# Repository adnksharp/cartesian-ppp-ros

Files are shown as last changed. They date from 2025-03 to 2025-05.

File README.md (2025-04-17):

# Cartesian Robot (PPP) ROS2

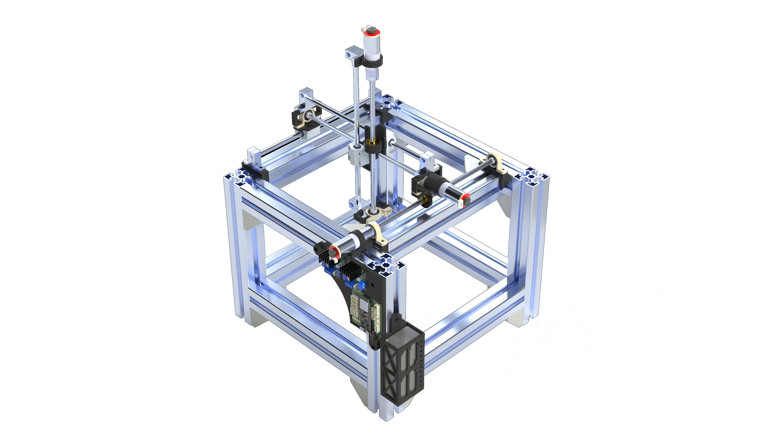
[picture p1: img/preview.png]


Robot cartesiano de 3 DOF con ROS2,

## Software y Hardware

<details>
    <summary>Software</summary>

* [ROS2 Jazzy](https://index.ros.org/p/desktop_full/#jazzy)
* [Gazebo Harmonic](https://gazebosim.org/docs/harmonic/getstarted/)
* [uROS Jazzy](https://github.com/micro-ROS/micro_ros_setup/tree/jazzy)
* [uROS Arduino Jazzy](https://github.com/micro-ROS/micro_ros_arduino/tree/jazzy)
* [KiCad](https://www.kicad.org)

</details>

<details>
    <summary>Componentes electrónicos</summary>

* 1 [ESP32 S3 WROOM 1 N16R8 DevKit](https://www.amazon.com/HiLetgo-ESP32-S3-ESP32-S3-DevKit-Bluetooth-Development/dp/B0CDWXWXCG)
* 2 [Módulos controladores de motores L298N](https://www.amazon.com/WWZMDiB-L298N-H-Bridge-Controller-Raspberry/dp/B0CR6BX5QL)
* 3 [Motores con encoder JGA25-371](https://www.amazon.com/JGA25-371-Encoder-Mounting-Bracket-Reduction/dp/B0CGLSGSZ7)
* 4 [LEDs 5730](https://www.amazon.com/AEDIKO-Lighting-Electronics-Components-Emitting/dp/B09XB5KDWS)
* 4 [Resistencias 220 Ohms 1206](https://www.amazon.com/Chanzon-Resistor-Tolerance-Resistors-Certificated/dp/B08R8CW7TX)
* 1 Fuente de alimentación 12V 2A

</details>

<details>
    <summary>Componentes mecánicos</summary>

* 12 perfiles de aluminio de 45x45x300 mm.
* 16 ángulos de aluminio de 45x45 mm.
* 3 tuercas de latón T8.
* 3 tornillos sin fin de 8x300 mm.
* 3 varillas lisas de 8x300 mm.
* 3 rodamientos SC8UU.
* 3 acopladores flexibles de 5x8 mm.
* 5 chumaceras KP08.
* 6 soportes SK8.
* Piezas impresas en 3D.

</details>

## Instalación
Para instalar el software de ROS2 Jazzy, se recomienda seguir la guía oficial de instalación de [ROS2](https://docs.ros.org/en/jazzy/Installation/Ubuntu-Install-Debs.html), el siguiente script instala el software de ROS2, Gazebo sim y micro-ROS en Ubuntu:

```shell
$SHELL ./src/install-ros.sh
```



Más información sobre el script en [src](src).

## Espacio de Trabajo de ROS2
Dentro de la carpeta ros-ws se encuentra el paquete en desarrollo `carobot`, el cual contiene los archivos para la visualización y simulación del robot cartesiano en Gazebo y RViz.

### Construcción del espacio de trabajo

```shell
cd ros-ws
colcon build
```

### Ejecución del lanzador

```shell
source install/setup.$(echo $SHELL | awk -F '/' '{print $NF}')
ros2 launch carobot display.launch.py
```

### Ejecución de la interfaz de usuario

```shell
source install/setup.$(echo $SHELL | awk -F '/' '{print $NF}')
ros2 run carobot pos_put.py
```

[ros-ws](ros-ws) contiene más información sobre el espacio de trabajo de ROS2.

## Electrónica
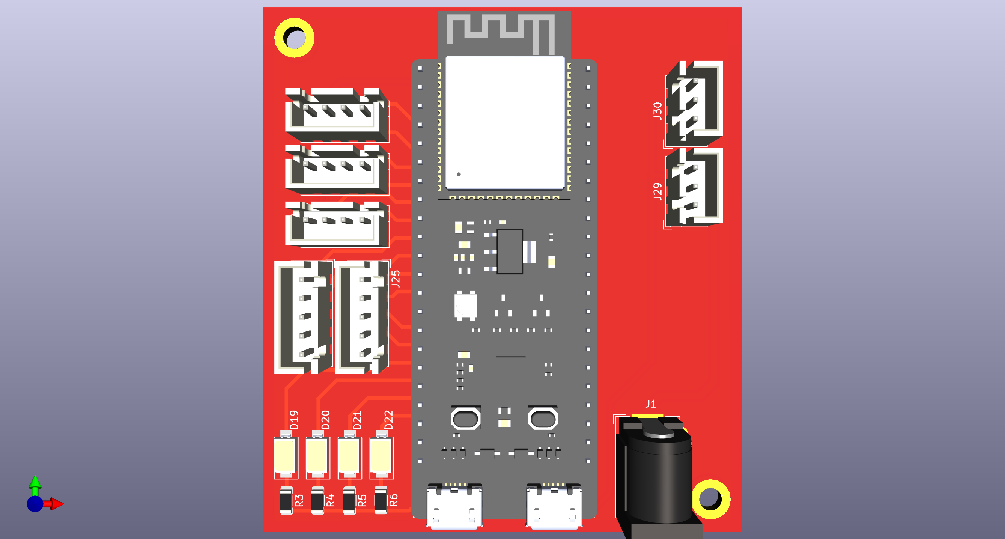
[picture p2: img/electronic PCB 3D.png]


[electronic](electronic) contiene el diseño de la PCB del robot cartesiano en formato KiCad, el cual incluye el diseño de la PCB y el esquema eléctrico.

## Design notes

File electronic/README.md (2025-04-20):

# Esquema elctrónico


El proyecto se desarrolló usando [KiCAD](https://www.kicad.org/). ([electronic.kicad_pro](electronic.kicad_pro)) se desarrollo para conectar una placa de ESP32 con 2 controladores de motores L298 y encoders de 3 motores JGA25-371. Los componentes utilizados en el proyecto son:

* 1 **ESP32 S3** WROOM 1 N16R8 DevKit
* 2 Modulos controladores de motores **L298**
* 3 Motores con encoder **JGA25-371**
* 4 LEDs
* 4 Resistencias **220 $\Omega$**
* 1 Fuente de alimentación **12V 2A**

## Esquema


El esquema eléctrico se encuentra dividido en ocho partes:

* 1 Alimentación: En esta sección se encuentra el conector de la fuente de alimentación para el circuito.
* 3 Motores
* 1 LED: LEDS conectados a los pines GPIO del microcontrolador y resistencias de 220 $\Omega$.
* 2 Controladores de motores
* 1 Microcontrolador

### Motores
En esta sección se encuentran los motores con encoder **JGA25-371**. 

* Las etiquetas del encoder se conectan a los pines GPIO del microcontrolador.
* Las etiquetas de alimentación se conectan a la salida de 3.3V del microcontrolador.
* Las etiquetas de los motores se conectan a los controladores de motores.

### Controladores de motores
En esta sección se encuentran los módulos de controladores de motores **L298N**. 

* Las etiquetas de los pines de control de los módulos se conectan a los pines GPIO del microcontrolador.
* Las etiquetas de alimentación se conectan a la fuente de alimentación y la salida de 5V de los controladores a la alimentación del microcontrolador.
* Las etiquetas de los motores se conectan a los motores.

### Microcontrolador
En esta sección se encuentra el microcontrolador **ESP32 S3** y las etiquetas de los pines que se utilizan para la comunicación con el resto de los componentes.

## PCB


La PCB fue diseñada para conectar todos los componentes del circuito. La PCB tiene un tamaño de 68.5x75 mm y fue diseñada para ser fabricada en dos capas. El diseño se encuentra en la carpeta `electronic` ([PCB.kicad_pcb](PCB.kicad_pcb)). Para la PCB se usan los siguientes componentes:

* 1 PCB de dos capas
* 1 Conector de alimentación **Barrel Jack**
* 2 Conectores **JST-B3B** para la alimentación de los controladores de motores.
* 3 Conectores **JST-B4B** para la conexión de los encoders de los motores.
* 2 Conectores **JST-B5B** para la conexión de los pines de control de los controladores de motores.
* 1 Terminal de 44 pines para la conexión del microcontrolador.
* 4 LEDs SMD **5730**
* 4 Resistencias 220 $\Omega$ SMD **1206**

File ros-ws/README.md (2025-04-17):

# Espacio de trabajo de ROS2


## carobot
El paquete `carobot` es un paquete de ROS2 para visualizar y simular el robot usando RViz2 y Gazebo. Este paquete incluye un modelo de robot y un archivo de lanzamiento.

### URDF
El modelo del robot se encuentra en el archivo `src/carobot/urdf/model.urdf`. Este archivo describe la geometría y la cinemática del robot. Las mallas usadas en el modelo se encuentran en la carpeta `src/carobot/urdf/meshes`. El archivo `model.urdf` es un archivo XML que describe el modelo del robot. Este archivo es usado por RViz2 y Gazebo para visualizar el robot.

### Lanzador
El archivo de lanzamiento `src/carobot/launch/display.launch.py` emplea los siguientes paquetes:

* `urdf_launch`: Carga el modelo del robot en RViz2.
* `ros_gz_sim`: Carga el modelo del robot en Gazebo a través de un tópico de ROS2 `/robot_description`.
* `ros_gz_bridge`: Crea un puente entre ROS2 y Gazebo para enviar datos de posición desde ROS2 y recibir datos de posición desde Gazebo. Este paquete es necesario para que el robot se mueva en Gazebo y para que los datos de posición se envíen a RViz2.
* `gz sim`: Abre un mundo vacío en Gazebo. Este mundo es usado para simular el robot.

### Scripts

#### pos_put.py
El archivo `src/carobot/src/pos_put.py` se encarga de leer los datos de posición deseados desde la terminal y enviarlos al robot. Este archivo usa el paquete `rclpy` para crear un nodo de ROS2 que se encarga de enviar los datos de posición al robot como `float64`.

#### pos_get.py
El archivo `src/carobot/src/pos_get.py` se encarga de leer los datos de posición del robot desde Gazebo y enviarlos a RViz2. Este archivo lee la posición de cada junta (`JointState`) del robot y la convierte en un mensaje con las posiciones de todas las juntas a un tópico de ROS2 `/joint_states`.

### Gazebo
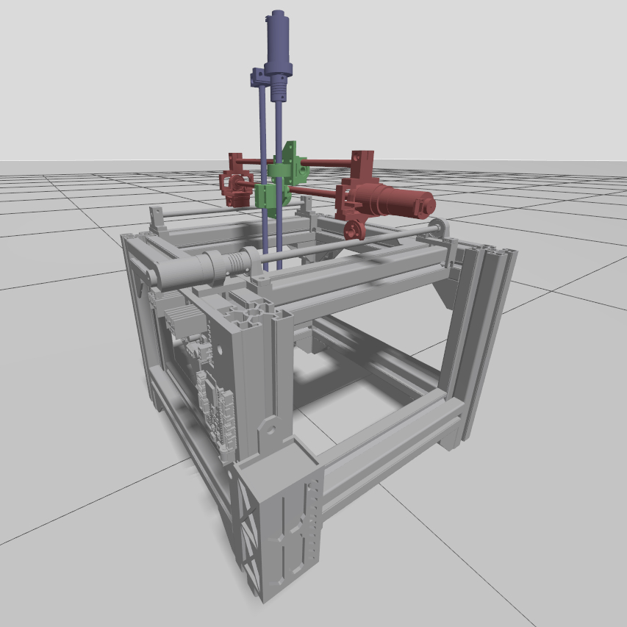
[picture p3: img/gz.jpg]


Al archivo URDF se le añadieron los siguientes plugins dentro de una etiqueta `<gazebo>`:

* `gz-sim-joint-state-publisher-system`: Este [plugin](https://gazebosim.org/api/sim/9/classgz_1_1sim_1_1systems_1_1JointStatePublisher.html) se encarga de publicar la posición de cada junta del robot en un tópico de gazebo puenteado a ROS2 `/world/empty/carobot/joint/prismatic_i_joint/state`. 
* `gz-sim-joint-position-controller-system`: Este [plugin](https://gazebosim.org/api/sim/9/jointcontrollers.html) se encarga de controlar la posición de cada junta del robot. Este plugin es necesario para que el robot se mueva en Gazebo. El plugin recibe los datos de posición desde el tópico `/world/empty/carobot/joint/prismatic_i_joint/cmd_pos` para aplicar un control de posición a la junta.

### RViz2
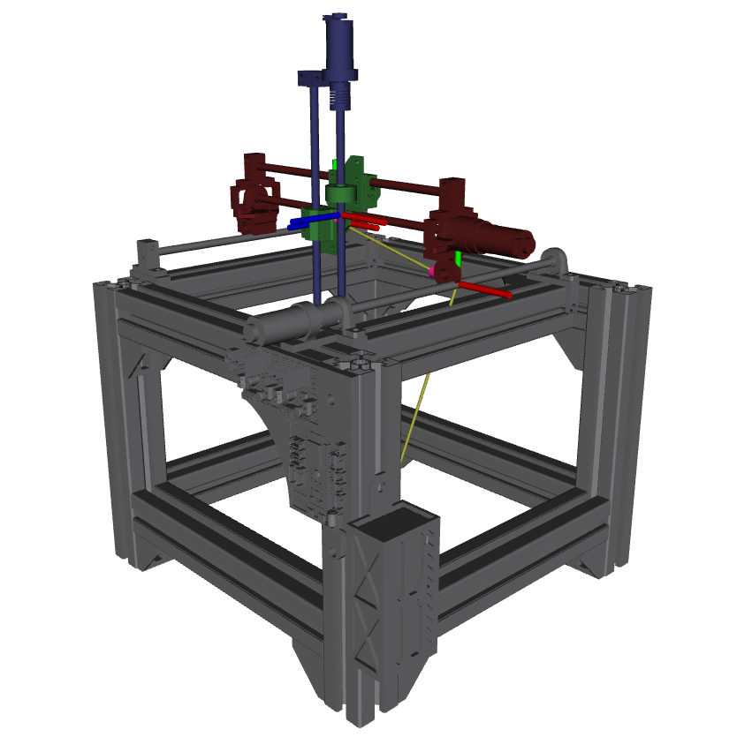
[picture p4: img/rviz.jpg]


El archivo `src/carobot/launch/display.launch.py` carga el modelo del robot en RViz2. Este archivo usa los paquetes `urdf_launch` y los tópicos `/robot_description` y `joint_states` para cargar el modelo del robot  y mover el robot en RViz2 respectivamente.

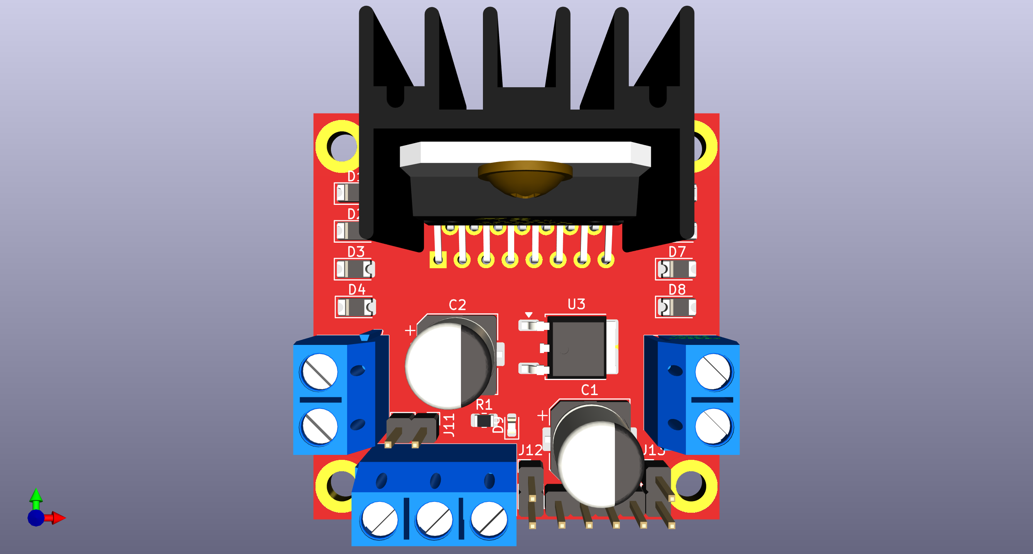
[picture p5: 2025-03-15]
img/L298N 3D.png

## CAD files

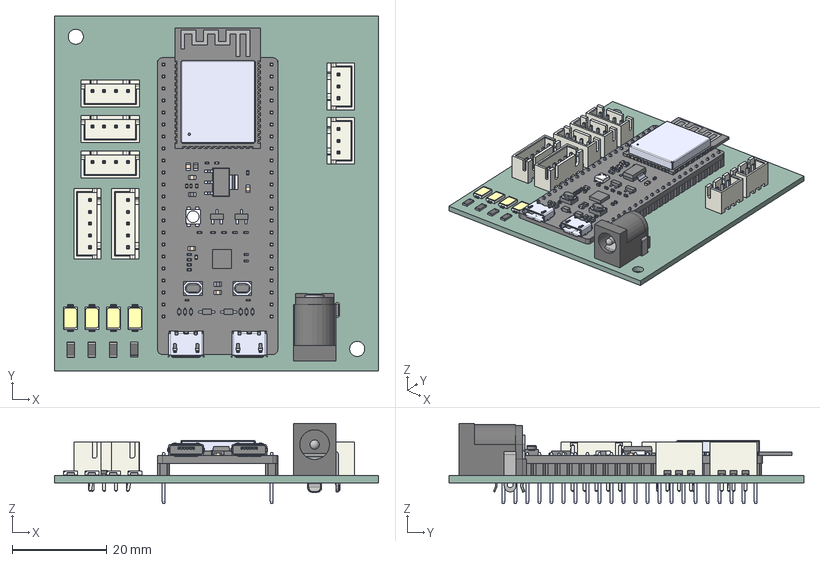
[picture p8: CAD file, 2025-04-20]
electronic/3D lib/PCB.step
68.5 x 75.0 x 17.0 mm
JST_XH_B5B-XH-A_1x05_P2.50mm_Vertical x 2
OF-SMD5730NW--3DModel-STEP-510211 x 4
JST_XH_B3B-XH-A_1x03_P2.50mm_Vertical x 2
R_1206_3216Metric x 4
JST_XH_B4B-XH-A_1x04_P2.50mm_Vertical x 3
BarrelJack_GCT_DCJ200-10-A_Horizontal
ESP32-S3-DevKitC-1-N16R8V--3DModel-STEP-269445
electronic_PCB

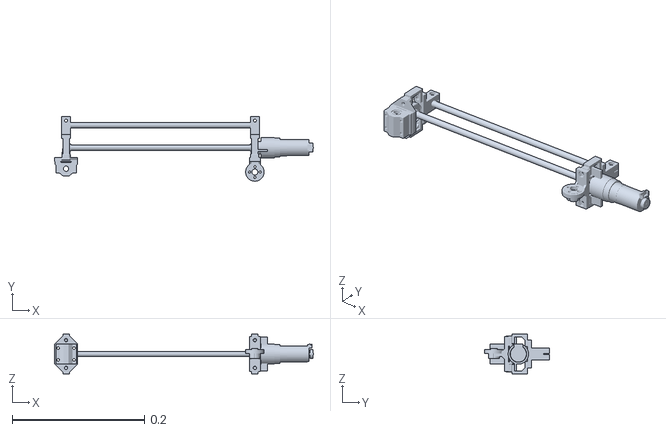
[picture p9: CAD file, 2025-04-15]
ros-ws/src/carobot/urdf/meshes/X.STL
0.392 x 0.0978 x 0.06

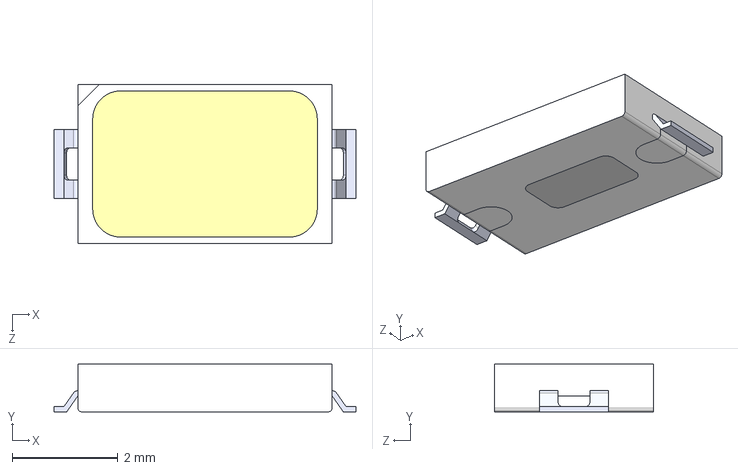
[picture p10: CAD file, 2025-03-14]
electronic/3D lib/OF-SMD5730NW--3DModel-STEP-510211.STEP
5.70 x 0.9 x 3.00 mm

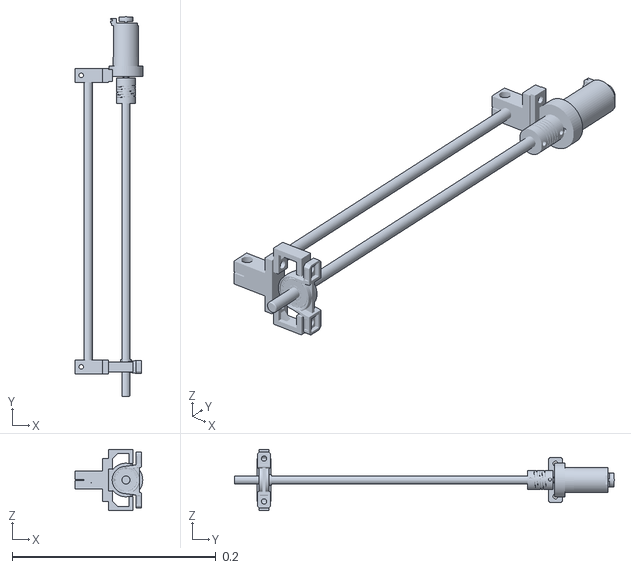
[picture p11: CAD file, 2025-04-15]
ros-ws/src/carobot/urdf/meshes/Y.STL
0.0663 x 0.373 x 0.06

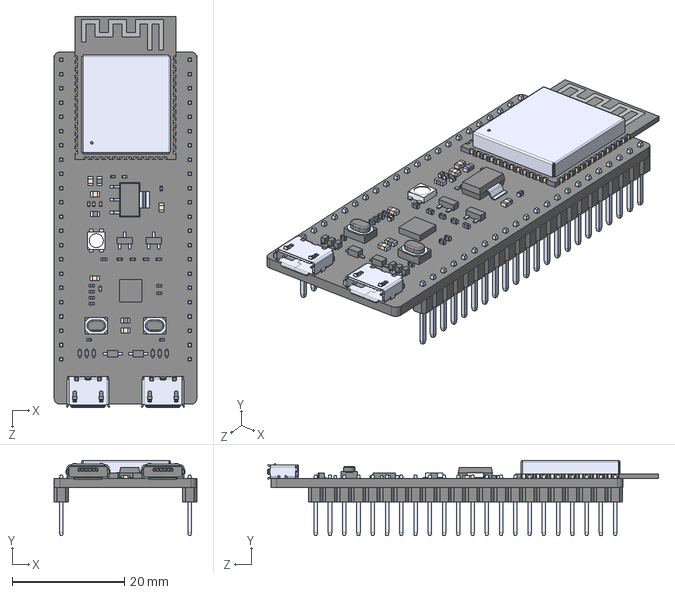
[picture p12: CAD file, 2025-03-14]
electronic/3D lib/ESP32-S3-DevKitC-1-N16R8V--3DModel-STEP-269445.STEP
25.4 x 13.4 x 69.6 mm

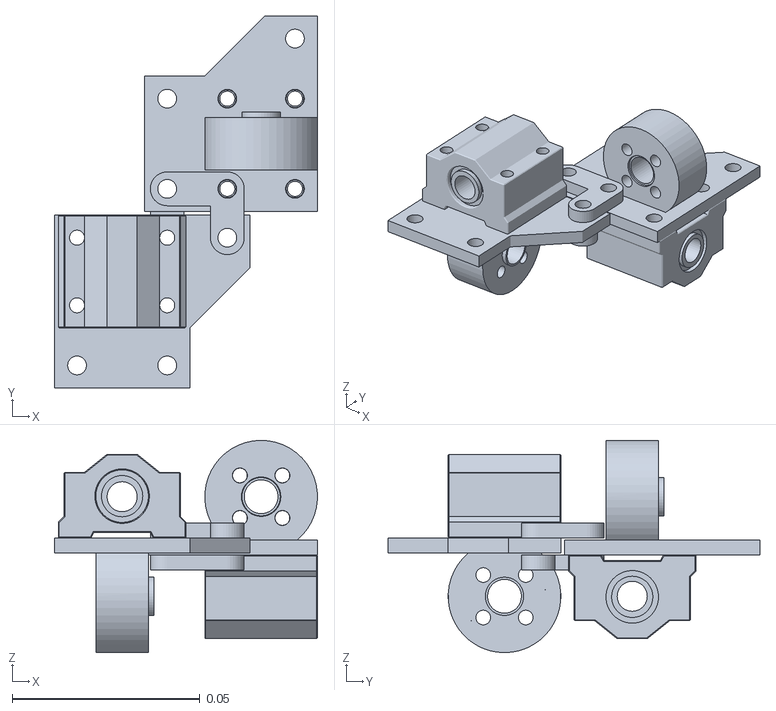
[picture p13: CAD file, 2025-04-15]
ros-ws/src/carobot/urdf/meshes/Z.STL
0.07 x 0.099 x 0.0565

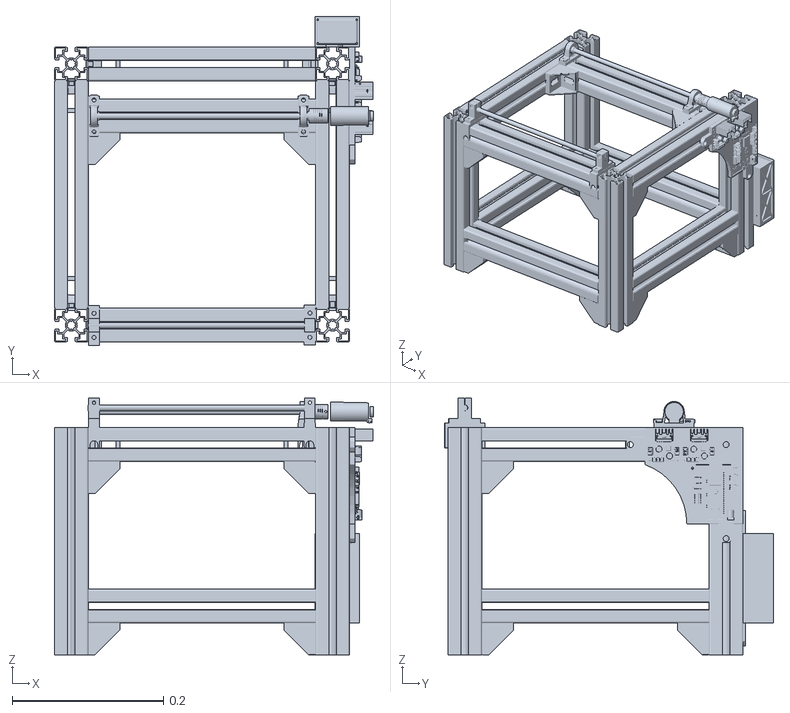
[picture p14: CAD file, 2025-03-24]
ros-ws/src/carobot/urdf/meshes/Base.STL
0.422 x 0.434 x 0.339

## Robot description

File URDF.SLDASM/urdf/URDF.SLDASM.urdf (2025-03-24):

<?xml version="1.0" encoding="utf-8"?>
<!-- This URDF was automatically created by SolidWorks to URDF Exporter! Originally created by Stephen Brawner (brawner@gmail.com) 
     Commit Version: 1.6.0-4-g7f85cfe  Build Version: 1.6.7995.38578
     For more information, please see http://wiki.ros.org/sw_urdf_exporter -->
<robot name="URDF.SLDASM">
  <link name="Link_Base">
    <inertial>
      <origin xyz="0.0114159508946672 0.175577206152015 0.00188434605031392" rpy="0 0 0" />
      <mass value="8.67596987352087" />
      <inertia ixx="0.299819303764689" ixy="-0.00525325844755418" ixz="0.0119696542324205" iyy="0.372411485126987" iyz="-0.010467275298787" izz="0.30471576885987" />
    </inertial>
    <visual>
      <origin xyz="0 0 0" rpy="0 0 0" />
      <geometry>
        <mesh filename="package://URDF.SLDASM/meshes/Link_Base.STL" />
      </geometry>
      <material name="">
        <color rgba="0.792156862745098 0.819607843137255 0.933333333333333 1" />
      </material>
    </visual>
    <collision>
      <origin xyz="0 0 0" rpy="0 0 0" />
      <geometry>
        <mesh filename="package://URDF.SLDASM/meshes/Link_Base.STL" />
      </geometry>
    </collision>
  </link>
  <link name="Link_X">
    <inertial>
      <origin xyz="-0.00188434605031393 0.175577206152015 0.0288296448289109" rpy="0 0 0" />
      <mass value="8.67596987352087" />
      <inertia ixx="0.30471576885987" ixy="0.010467275298787" ixz="-0.0119696542324205" iyy="0.372411485126987" iyz="-0.00525325844755414" izz="0.299819303764689" />
    </inertial>
    <visual>
      <origin xyz="0 0 0" rpy="0 0 0" />
      <geometry>
        <mesh filename="package://URDF.SLDASM/meshes/Link_X.STL" />
      </geometry>
      <material name="">
        <color rgba="0.792156862745098 0.819607843137255 0.933333333333333 1" />
      </material>
    </visual>
    <collision>
      <origin xyz="0 0 0" rpy="0 0 0" />
      <geometry>
        <mesh filename="package://URDF.SLDASM/meshes/Link_X.STL" />
      </geometry>
    </collision>
  </link>
  <joint name="J1" type="prismatic">
    <origin xyz="-0.017414 0 0" rpy="1.5708 0 1.5708" />
    <parent link="Link_Base" />
    <child link="Link_X" />
    <axis xyz="0 0 1" />
    <limit lower="0" upper="0" effort="0" velocity="0" />
    <dynamics damping="0.01" friction="0.01" />
  </joint>
  <link name="Link_Z">
    <inertial>
      <origin xyz="0.0850555171017934 0.175577206152015 0.00991818358297185" rpy="0 0 0" />
      <mass value="8.67596987352087" />
      <inertia ixx="0.30471576885987" ixy="0.010467275298787" ixz="-0.0119696542324205" iyy="0.372411485126987" iyz="-0.00525325844755414" izz="0.299819303764689" />
    </inertial>
    <visual>
      <origin xyz="0 0 0" rpy="0 0 0" />
      <geometry>
        <mesh filename="package://URDF.SLDASM/meshes/Link_Z.STL" />
      </geometry>
      <material name="">
        <color rgba="0.792156862745098 0.819607843137255 0.933333333333333 1" />
      </material>
    </visual>
    <collision>
      <origin xyz="0 0 0" rpy="0 0 0" />
      <geometry>
        <mesh filename="package://URDF.SLDASM/meshes/Link_Z.STL" />
      </geometry>
    </collision>
  </link>
  <joint name="J2" type="prismatic">
    <origin xyz="-0.08694 0 0.018911" rpy="0 0 0" />
    <parent link="Link_X" />
    <child link="Link_Z" />
    <axis xyz="1 0 0" />
    <limit lower="0" upper="0" effort="0" velocity="0" />
    <dynamics damping="0.01" friction="0.01" />
  </joint>
  <link name="Link_Y">
    <inertial>
      <origin xyz="0.0565709384857237 0.073229775350901 0.00991818358297399" rpy="0 0 0" />
      <mass value="8.67596987352087" />
      <inertia ixx="0.30471576885987" ixy="0.0104672752987869" ixz="-0.0119696542324205" iyy="0.372411485126987" iyz="-0.00525325844755413" izz="0.299819303764689" />
    </inertial>
    <visual>
      <origin xyz="0 0 0" rpy="0 0 0" />
      <geometry>
        <mesh filename="package://URDF.SLDASM/meshes/Link_Y.STL" />
      </geometry>
      <material name="">
        <color rgba="0.792156862745098 0.819607843137255 0.933333333333333 1" />
      </material>
    </visual>
    <collision>
      <origin xyz="0 0 0" rpy="0 0 0" />
      <geometry>
        <mesh filename="package://URDF.SLDASM/meshes/Link_Y.STL" />
      </geometry>
    </collision>
  </link>
  <joint name="J3" type="prismatic">
    <origin xyz="0.028485 0.10235 0" rpy="0 0 0" />
    <parent link="Link_Z" />
    <child link="Link_Y" />
    <axis xyz="0 1 0" />
    <limit lower="0" upper="0" effort="0" velocity="0" />
    <dynamics damping="0.01" friction="0.01" />
  </joint>
</robot>

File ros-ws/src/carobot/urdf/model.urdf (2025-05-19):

<?xml version="1.0" encoding="utf-8"?>
<robot name="CartesianRobot">
  <link name="base_link">
    <inertial>
      <origin xyz="0.001 0.01 0.16" rpy="0 0 0" />
      <mass value="8.22" />
	  <inertia ixx="0.30471576885987" ixy="0.010467275298787" ixz="-0.0119696542324205" iyy="0.372411485126987" iyz="-0.00525325844755414" izz="0.299819303764689" />
    </inertial>
    <visual>
      <origin xyz="0 0 0" rpy="0 0 0" />
      <geometry>
        <mesh filename="file://$(find carobot)/urdf/meshes/Base.STL" />
      </geometry>
      <material name="">
        <color rgba="0.49 0.49 0.5 1" />
      </material>
    </visual>
    <collision>
      <origin xyz="0 0 0" rpy="0 0 0" />
      <geometry>
        <mesh filename="file://$(find carobot)/urdf/meshes/Base.STL" />
      </geometry>
    </collision>
  </link>
  <link name="prismatic_0">
    <inertial>
      <origin xyz="-0.069 0.045 0" rpy="0 0 0" />
      <mass value="0.398" />
	  <inertia ixx="0.30471576885987" ixy="0.010467275298787" ixz="-0.0119696542324205" iyy="0.372411485126987" iyz="-0.00525325844755414" izz="0.299819303764689" />
    </inertial>
    <visual>
      <origin xyz="-0.3035 -0.3215 -0.03" rpy="0 0 0" />
      <geometry>
        <mesh filename="file://$(find carobot)/urdf/meshes/X.STL" />
      </geometry>
      <material name="">
        <color rgba="0.40 0.12 0.12 1" />
      </material>
    </visual>
    <collision>
      <origin xyz="-0.3035 -0.3215 -0.03" rpy="0 0 0" />
      <geometry>
        <mesh filename="file://$(find carobot)/urdf/meshes/X.STL" />
      </geometry>
    </collision>
  </link>
  <joint name="prismatic_0_joint" type="prismatic">
    <origin xyz="0.1135 0 0.3215" rpy="1.5708 0 0" />
    <parent link="base_link" />
    <child link="prismatic_0" />
    <axis xyz="0 0 -1" />
    <limit lower="-0.104" upper="0.09" effort="5e3" velocity="20" />
    <dynamics damping="0.01" friction="0.1" />
  </joint>
  <transmission name="trans_prismatic_0_joint">
    <type>transmission_interface/SimpleTransmission</type>
    <joint name="prismatic_0_joint">
      <hardwareInterface>hardware_interface/PositionJointInterface</hardwareInterface>
    </joint>
    <actuator name="motor_prismatic_0_joint">
      <hardwareInterface>hardware_interface/PositionJointInterface</hardwareInterface>
	  <mechanicalReduction>8</mechanicalReduction>
    </actuator>
  </transmission>
  <link name="prismatic_1">
    <inertial>
      <origin xyz="0.02 0.015 0.012" rpy="0 0 0" />
      <mass value="0.08073" />
      <inertia ixx="0.30471576885987" ixy="0.010467275298787" ixz="-0.0119696542324205" iyy="0.372411485126987" iyz="-0.00525325844755414" izz="0.299819303764689" />
    </inertial>
    <visual>
      <origin xyz="-0.018 -0.3581 -0.0225" rpy="0 0 0" />
      <geometry>
        <mesh filename="file://$(find carobot)/urdf/meshes/Z.STL" />
      </geometry>
      <material name="">
        <color rgba="0.22 0.49 0.22 1" />
      </material>
    </visual>
    <collision>
      <origin xyz="-0.018 -0.3581 -0.0225" rpy="0 0 0" />
      <geometry>
        <mesh filename="file://$(find carobot)/urdf/meshes/Z.STL" />
      </geometry>
    </collision>
  </link>
  <joint name="prismatic_1_joint" type="prismatic">
    <origin xyz="-0.1628 0.0365 0.0005" rpy="0 0 0" />
    <parent link="prismatic_0" />
    <child link="prismatic_1" />
    <axis xyz="1 0 0" />
    <limit lower="-0.0865" upper="0.0865" effort="5e3" velocity="20" />
    <dynamics damping="0.01" friction="0.1" />
  </joint>
  <transmission name="trans_prismatic_1_joint">
    <type>transmission_interface/SimpleTransmission</type>
    <joint name="prismatic_1_joint">
      <hardwareInterface>hardware_interface/PositionJointInterface</hardwareInterface>
    </joint>
    <actuator name="motor_prismatic_1_joint">
      <hardwareInterface>hardware_interface/PositionJointInterface</hardwareInterface>
      <mechanicalReduction>8</mechanicalReduction>
    </actuator>
  </transmission>
  <link name="prismatic_2">
    <inertial>
      <origin xyz="-0.015 0.055 0.00" rpy="0 0 0" />
      <mass value=".030612" />
      <inertia ixx="0.30471576885987" ixy="0.0104672752987869" ixz="-0.0119696542324205" iyy="0.372411485126987" iyz="-0.00525325844755413" izz="0.299819303764689" />
    </inertial>
    <visual>
      <origin xyz="-0.05 -0.419 -0.0485" rpy="0 0 0" />
      <geometry>
        <mesh filename="file://$(find carobot)/urdf/meshes/Y.STL" />
      </geometry>
      <material name="">
        <color rgba="0.22 0.22 0.43 1" />
      </material>
    </visual>
    <collision>
      <origin xyz="-0.05 -0.419 -0.0485" rpy="0 0 0" />
      <geometry>
        <mesh filename="file://$(find carobot)/urdf/meshes/Y.STL" />
      </geometry>
    </collision>
  </link>
  <joint name="prismatic_2_joint" type="prismatic">
    <origin xyz="0.037 0.0345 0.026" rpy="0 0 0" />
    <parent link="prismatic_1" />
    <child link="prismatic_2" />
    <axis xyz="0 -1 0" />
    <limit lower="-0.0889" upper="0.0889" effort="5e3" velocity="20" />
    <dynamics damping="0.01" friction="0.1" />
  </joint>
  <transmission name="trans_prismatic_2_joint">
    <type>transmission_interface/SimpleTransmission</type>
    <joint name="prismatic_2_joint">
      <hardwareInterface>hardware_interface/PositionJointInterface</hardwareInterface>
    </joint>
    <actuator name="motor_prismatic_2_joint">
      <hardwareInterface>hardware_interface/PositionJointInterface</hardwareInterface>
      <mechanicalReduction>8</mechanicalReduction>
    </actuator>
  </transmission>
  <gazebo>
	  <plugin filename="gz-sim-joint-state-publisher-system" name="gz::sim::systems::JointStatePublisher">
		  <joint_name>prismatic_0_joint</joint_name>
		  <topic>yoba/carobot/joint_0/state</topic>
	  </plugin>
	  <plugin filename="gz-sim-joint-state-publisher-system" name="gz::sim::systems::JointStatePublisher">
		  <joint_name>prismatic_1_joint</joint_name>
		  <topic>yoba/carobot/joint_1/state</topic>
	  </plugin>
	  <plugin filename="gz-sim-joint-state-publisher-system" name="gz::sim::systems::JointStatePublisher">
		  <joint_name>prismatic_2_joint</joint_name>
		  <topic>yoba/carobot/joint_2/state</topic>
	  </plugin>
  	  <plugin filename="gz-sim-joint-position-controller-system" name="gz::sim::systems::JointPositionController">
        <joint_name>prismatic_0_joint</joint_name>
		<topic>yoba/carobot/joint_0/cmd_pos</topic>
		<p_gain>68.21</p_gain>
        <i_gain>0.56</i_gain>
        <d_gain>34.14</d_gain>
	  </plugin>
  	  <plugin filename="gz-sim-joint-position-controller-system" name="gz::sim::systems::JointPositionController">
        <joint_name>prismatic_1_joint</joint_name>
		<topic>yoba/carobot/joint_1/cmd_pos</topic>
		<p_gain>68.21</p_gain>
        <i_gain>0.56</i_gain>
        <d_gain>34.14</d_gain>
	  </plugin>
  	  <plugin filename="gz-sim-joint-position-controller-system" name="gz::sim::systems::JointPositionController">
        <joint_name>prismatic_2_joint</joint_name>
		<topic>yoba/carobot/joint_2/cmd_pos</topic>
		<p_gain>68.21</p_gain>
        <i_gain>0.56</i_gain>
        <d_gain>34.14</d_gain>
	  </plugin>
  </gazebo>
</robot>

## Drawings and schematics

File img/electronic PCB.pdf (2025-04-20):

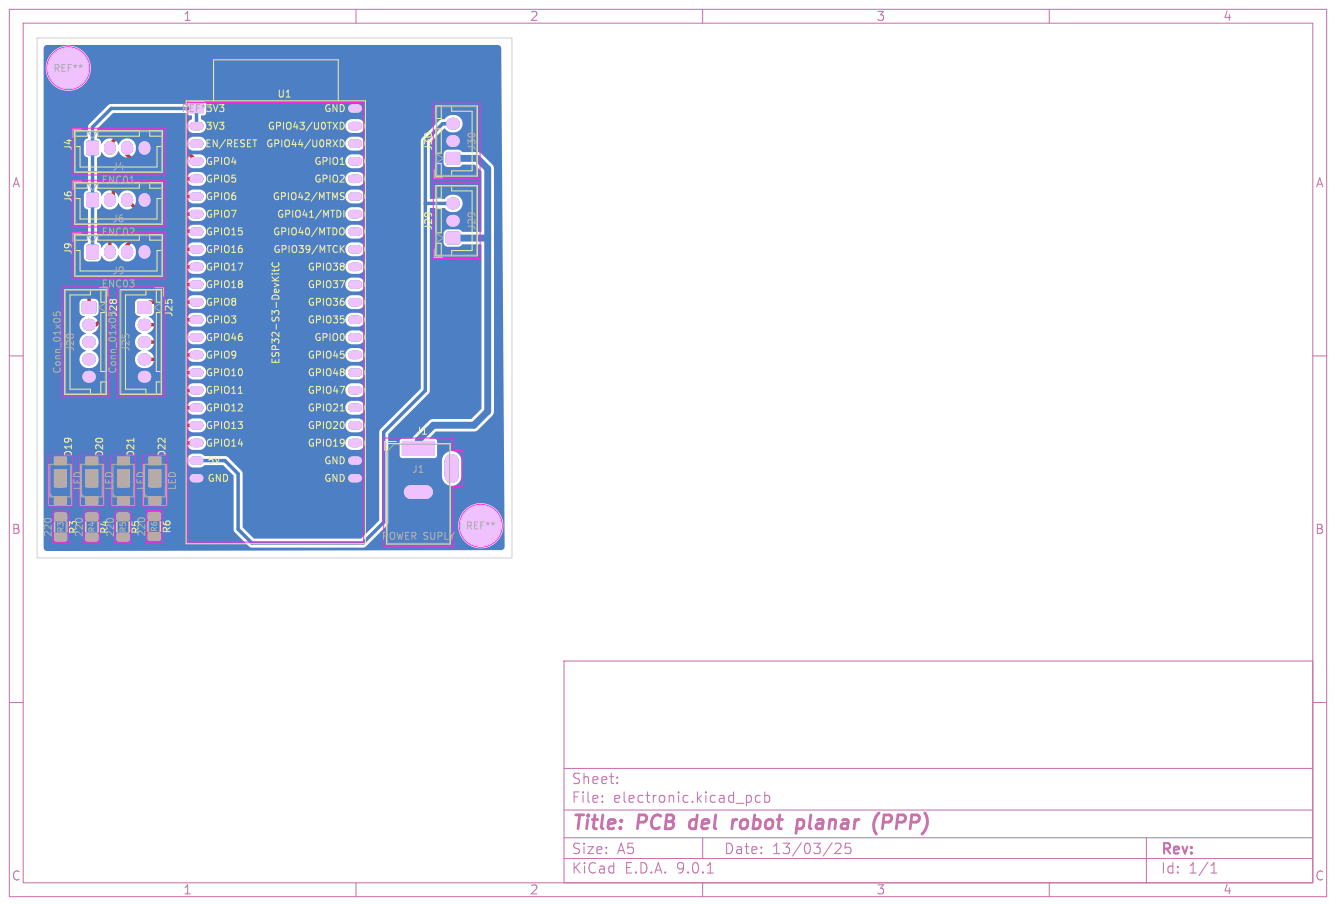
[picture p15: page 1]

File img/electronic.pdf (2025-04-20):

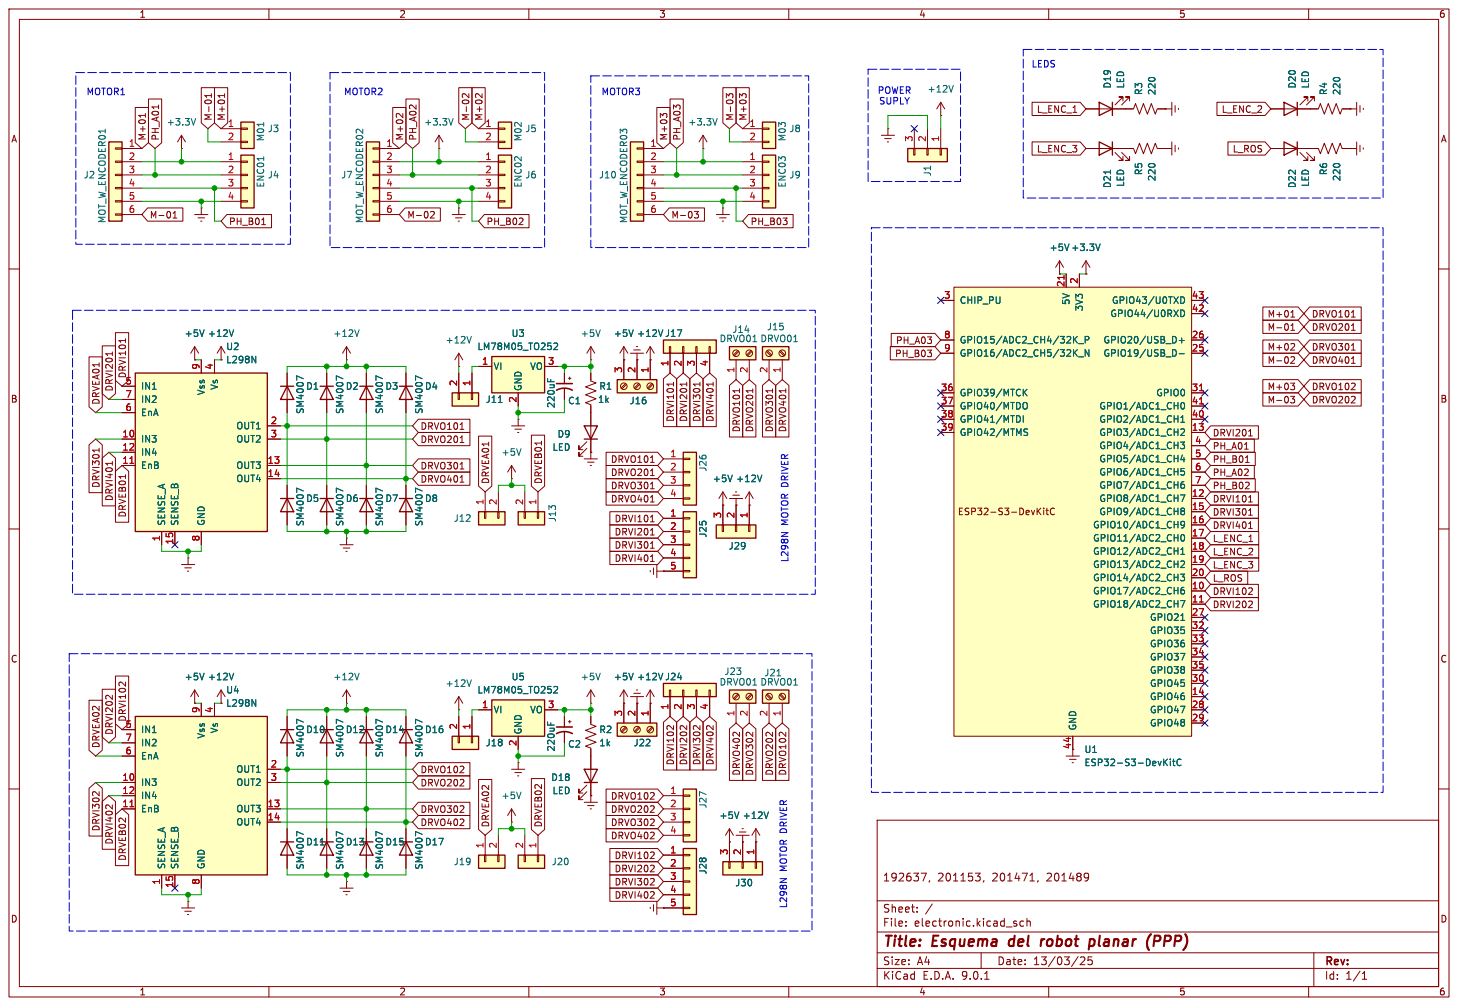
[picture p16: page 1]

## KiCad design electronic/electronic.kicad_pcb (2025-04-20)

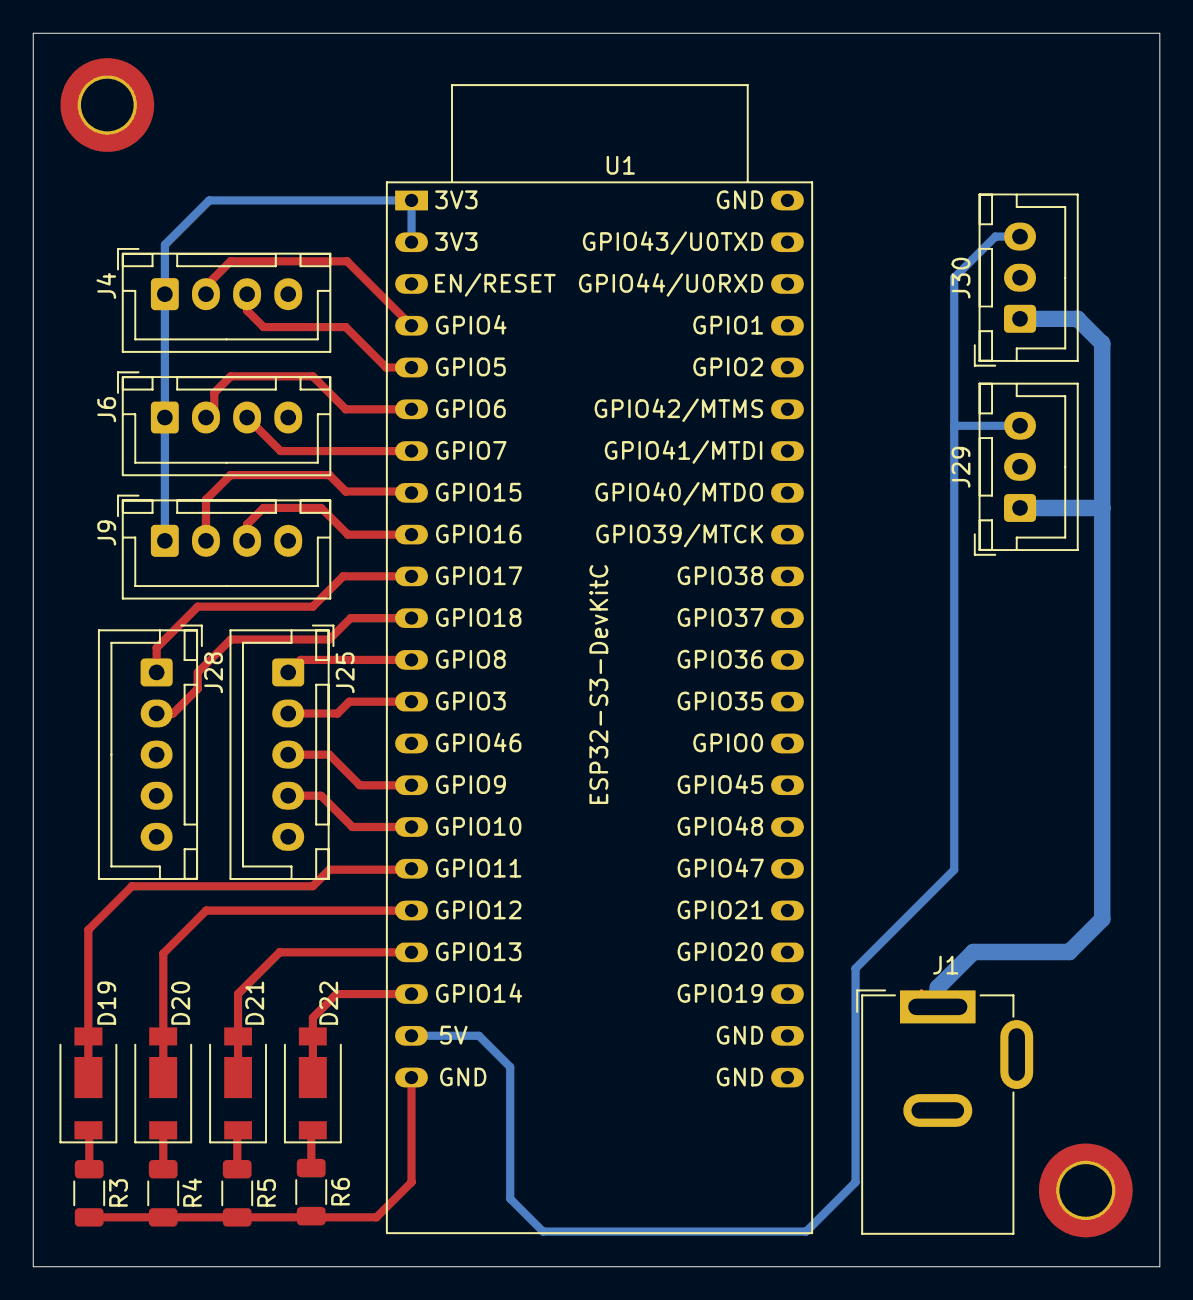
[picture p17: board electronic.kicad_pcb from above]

Board: 2 copper layers, 68.5 x 75.0 mm, 17 parts (0 on the bottom side), 24 nets.

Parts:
D19, D20, D21, D22: LED; LED_Yuji_5730
J1: POWER SUPLY; BarrelJack_GCT_DCJ200-10-A_Horizontal
J4: ENC01; JST_XH_B4B-XH-A_1x04_P2.50mm_Vertical
J6: ENC02; JST_XH_B4B-XH-A_1x04_P2.50mm_Vertical
J9: ENC03; JST_XH_B4B-XH-A_1x04_P2.50mm_Vertical
J25, J28: Conn_01x05; JST_XH_B5B-XH-A_1x05_P2.50mm_Vertical
J29, J30: Screw_Terminal_01x03; JST_XH_B3B-XH-A_1x03_P2.50mm_Vertical
R3, R4, R5, R6: 220; R_1206_3216Metric
U1: ESP32-S3-DevKitC

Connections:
+3.3V: J4.1, J6.1, J9.1, U1.1 (3V3), U1.2 (3V3)
+5V: J29.3, J30.3, U1.21 (5V)
+12V: J1.1, J29.1, J30.1
DRVI101: J25.1, U1.12 (GPIO8/ADC1_CH7)
DRVI102: J28.1, U1.10 (GPIO17/ADC2_CH6)
DRVI201: J25.2, U1.13 (GPIO3/ADC1_CH2)
DRVI202: J28.2, U1.11 (GPIO18/ADC2_CH7)
DRVI301: J25.3, U1.15 (GPIO9/ADC1_CH8)
DRVI401: J25.4, U1.16 (GPIO10/ADC1_CH9)
Earth: J1.2, J4.4, J6.4, J9.4, J25.5, J28.5, J29.2, J30.2, R3.2, R4.2, R5.2, R6.2, U1.22 (GND), U1.23 (GND), U1.24 (GND), U1.44 (GND)
L_ENC_1: D19.2 (A), U1.17 (GPIO11/ADC2_CH0)
L_ENC_2: D20.2 (A), U1.18 (GPIO12/ADC2_CH1)
L_ENC_3: D21.2 (A), U1.19 (GPIO13/ADC2_CH2)
L_ROS: D22.2 (A), U1.20 (GPIO14/ADC2_CH3)
unnamed: D19.1 (K), R3.1
unnamed: D20.1 (K), R4.1
unnamed: D21.1 (K), R5.1
unnamed: D22.1 (K), R6.1
PH_A01: J4.2, U1.4 (GPIO4/ADC1_CH3)
PH_A02: J6.2, U1.6 (GPIO6/ADC1_CH5)
PH_A03: J9.2, U1.8 (GPIO15/ADC2_CH4/32K_P)
PH_B01: J4.3, U1.5 (GPIO5/ADC1_CH4)
PH_B02: J6.3, U1.7 (GPIO7/ADC1_CH6)
PH_B03: J9.3, U1.9 (GPIO16/ADC2_CH5/32K_N)

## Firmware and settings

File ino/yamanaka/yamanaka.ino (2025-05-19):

#include <Ticker.h>
//Hardware config
const byte led[4] = {11, 12, 13, 14};
const byte motor[3][2] = {
	{17,18}, // 190
	{10, 9}, // 164
	{8, 3}
}, encoder[3][2] = {
	{5, 4},
	{6, 7},
	{16, 15}
};

//Encoder
volatile long position[3] = {0, 0, 0};
float setpoint[3] = {0, 0, 0};

//PID 
Ticker PIDTicker;
int sampleTime = 100;
double Kp[3] = {0.375, 0.375, 0.375},
		Ki[3] = {0.0974, 0.0974, 0.0974},
		Kd[3] = {0.01, 0.01, 0.01},
		KpError[3] = {0, 0, 0},
		KiError[3] = {0, 0, 0},
		KdError[3] = {0, 0, 0},
		CacheError[3] = {0, 0, 0},
		output[3] = {0, 0, 0};
float outMin[3] = {-255, -255, -255},
		outMax[3] = {255, 255, 255}, //+813, -970
		PPMM[3] = {12.1, 12.1, 118.7}; // pulse per millimeters
int PWM[3] = {0, 0, 0},
	minPWM[3] = {98, 102, 39},
	PPR[3] = {22, 22, 22}; // pulse per revolution
		//mPr[3] = {8, 8, 8}; // milimeters per revolution

void PID()
{
	for(byte i = 0; i < 3; i++)
	{
		double pos, error;
		pos = float(position[i]) / PPMM[i];
		error = setpoint[i] - pos;
		KpError[i] = Kp[i] * error;
		KiError[i] += Ki[i] * error * (sampleTime / 1000.0);
		KiError[i] = constrain(KiError[i], outMin[i], outMax[i]);
		KdError[i] = Kd[i] * (error - CacheError[i]) / (sampleTime / 1000.0);
		CacheError[i] = error;

		output[i] = KpError[i] + KiError[i] + KdError[i];
		output[i] = constrain(output[i], outMin[i], outMax[i]);

		if(output[i] > outMax[i])
			output[i] = outMax[i];
		else if(output[i] < outMin[i])
			output[i] = outMin[i];

		PWM[i] = output[i];
		if(PWM[i] > 0 && PWM[i] < minPWM[i])
			PWM[i] += minPWM[i];
		else if(PWM[i] < 0 && PWM[i] > -minPWM[i])
			PWM[i] -= minPWM[i];
		analogWrite(motor[i][0], PWM[i] > 0 ? PWM[i] : 0);
		analogWrite(motor[i][1], PWM[i] < 0 ? -PWM[i] : 0);
		digitalWrite(led[i], PWM[i] != 0);
	}
}

void encoderA()
{
	if(digitalRead(encoder[0][0]) == digitalRead(encoder[0][1]))
		position[0]++;
	else
		position[0]--;
}

void encoderB()
{
	if(digitalRead(encoder[1][0]) == digitalRead(encoder[1][1]))
		position[1]++;
	else
		position[1]--;
}

void encoderC()
{
	if(digitalRead(encoder[2][0]) == digitalRead(encoder[2][1]))
		position[2]++;
	else
		position[2]--;
}

void serialEvent()
{
	if (Serial.available() > 0)
	{
		String command = Serial.readStringUntil('\n');
		int separatorIndex = command.indexOf(':');
		if (separatorIndex != -1)
		{
			int motorIndex = command.substring(0, separatorIndex).toInt();
			int value = command.substring(separatorIndex + 1).toInt();
			Serial.println("Motor: " + String(motorIndex) + ", Value: " + String(value));
			if (motorIndex >= 0 && motorIndex < 3)
				setpoint[motorIndex] = value;
			else
				Serial.println("Invalid motor index");
		}
		else
		{
			Serial.println("Invalid command format");
		}
	}
}

void setup()
{
	Serial.begin(115200);

	for(size_t i = 0; i < sizeof(encoder) / sizeof(encoder[0]); i++)
		for(byte j = 0; j < 2; j++)
			pinMode(encoder[i][j], INPUT);
	for(size_t i = 0; i < sizeof(motor) / sizeof(motor[0]); i++)
		for(byte j = 0; j < 2; j++)
			pinMode(motor[i][j], OUTPUT);
	for(byte i: led)
		pinMode(i, OUTPUT);

	attachInterrupt(digitalPinToInterrupt(encoder[0][0]), encoderA, CHANGE);
	attachInterrupt(digitalPinToInterrupt(encoder[1][0]), encoderB, CHANGE);
	attachInterrupt(digitalPinToInterrupt(encoder[2][0]), encoderC, CHANGE);

	PIDTicker.attach_ms(sampleTime, PID);
	digitalWrite(RGB_BUILTIN, LOW);
}

void loop()
{
	Serial.println(
		"[ " + String(setpoint[0]) +
		" | " + String(position[0] / PPMM[0]) + " | " +
		String(PWM[0]) + " ] [ " + String(setpoint[1]) +
		" | " + String(position[1] / PPMM[1]) + " | " +
		String(PWM[1]) + " ] [ " + String(setpoint[2]) +
		" | " + String(position[2] / PPMM[2]) + " | " +
		String(PWM[2]) + " ]"
	);
	delay(50);
}

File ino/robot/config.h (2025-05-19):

// hardware definitions
#ifdef RGB_BUILTIN
byte LED[6] = {11, 12, 13, 14, LED_BUILTIN, RGB_BUILTIN};
#else
byte LED[6] = {11, 12, 13, 14, 2, 0};
#endif
byte MOTOR[3][2] = {
	{17, 18},
	{10, 9},
	{8, 3}
}, ENCODER[3][2] = {
	{5, 4},
	{6, 7},
	{16, 15}
};

int motorMin[3] = {98, 102, 39};
float PPMM[3] = {12.1, 12.1, 118.7};

// pid config
double kp[3] = {0.375, 0.375, 0.375},
	   ki[3] = {0.0974, 0.0974, 0.0974},
	   kd[3] = {0.01, 0.01, 0.01};

// uROS configurations
char *NODE_NAME  = "sensiact",
	 *TOPIC_PUB = "yoba/sensiact/info",
	 *TOPIC_ECHO = "yoba/sensiact/cmd_pos";

byte timeout = 100;

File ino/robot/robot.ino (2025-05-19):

#include "config.h"
#include "encoder.h"
#include "pid.h"
#include "times.h"
#include "leds.h"
#include "uros.h"

extern byte LED[6];
extern byte MOTOR[3][2];
extern byte ENCODER[3][2];

LEDs led;
UROS ros;
Motor motor;
PID pid;
Ticker PIDTicker;

extern void calc();
extern void M1Update();
extern void M2Update();
extern void M3Update();
extern void err(bool rgb, bool fail);

void subscription_callback(const void * msgin)
{
	const std_msgs__msg__Int16MultiArray * msg = (const std_msgs__msg__Int16MultiArray *)msgin;
	if(int(pid.output[0] + pid.output[1] + pid.output[2]) != 0)
		return;
	for (int i = 0; i < 3; i++)
	{
		float val = msg->data.data[i];
		pid.setpoint[i] = val;
	}
}

void setup() 
{
	led.begin(LED);
	led.set(0, HIGH);

	ros.begin(NODE_NAME);
	/*
		/yoba/sensiact/info
		pos[0],
		pos[1],
		pos[2],
		err,
	*/
	led.set(1, HIGH);
	ros.make_multi_int16(TOPIC_PUB, 4, ros.topic_pub);
	led.set(2, HIGH);
	/*
		/yoba/sensiact/cmd_pos
		sp[0],
		sp[1],
		sp[2],
		sp[3]
	*/
	ros.echo_multi_int16(TOPIC_ECHO, ros.topic_sub, ros.multi_int16_msg);

	RCCHECK(rclc_executor_init(&ros.executor, &ros.support.context, 1, &ros.allocator));
	RCCHECK(rclc_executor_add_subscription(&ros.executor, &ros.topic_sub, &ros.multi_int16_msg, &subscription_callback, ON_NEW_DATA));

	led.set(0, LOW);
	led.set(1, LOW);
	led.set(2, LOW);
	motor.begin(ENCODER, MOTOR);
	pid.begin(kp, ki, kd, PPMM, motorMin);
	PIDTicker.attach_ms(pid.sample, calc);
}

void loop()
{
	led.set(3, HIGH);
	int16_t post[4] = {
		int(motor.pos[0] / pid.PPMM[0]),
		int(motor.pos[1] / pid.PPMM[1]),
		int(motor.pos[2] / pid.PPMM[2]),
		int(pid.output[0] + pid.output[1] + pid.output[2])
	};
	ros.post_multi_int16(post, 4, ros.topic_pub);
	RCCHECK(rclc_executor_spin_some(&ros.executor, RCL_MS_TO_NS(timeout)));
	led.set(3, LOW);
	delay(150);
}

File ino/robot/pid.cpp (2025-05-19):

#include "pid.h"
#include "encoder.h"

extern Motor motor;
extern PID pid;

void calc()
{
	for (byte i = 0; i < 3; i++)
	{
		double pos, error;
		pos = float(motor.pos[i]) / pid.PPMM[i];
		error = pid.setpoint[i] - pos;
		
		pid.KpError[i] = pid.Kp[i] * error;
		pid.KiError[i] += pid.Ki[i] * error * (pid.sample / 1000.0);
		pid.KiError[i] = constrain(pid.KiError[i], pid.outMin, pid.outMax);
		pid.KdError[i] = pid.Kd[i] * (error - pid.CacheError[i]) / (pid.sample / 1000.0);
		pid.CacheError[i] = error;
		
		pid.output[i] = pid.KpError[i] + pid.KiError[i] + pid.KdError[i];
		pid.output[i] = constrain(pid.output[i], pid.outMin, pid.outMax);

		if(pid.output[i] < pid.outMin)
			pid.output[i] = pid.outMin;
		if(pid.output[i] > pid.outMax)
			pid.output[i] = pid.outMax;

		pid.PWM[i] = pid.output[i];
		if(pid.PWM[i] > 0 && pid.PWM[i] < pid.minPWM[i])
			pid.PWM[i] += pid.minPWM[i];
		else if(pid.PWM[i] < 0 && pid.PWM[i] > -pid.minPWM[i])
			pid.PWM[i] -= pid.minPWM[i];

		motor.set(i, pid.PWM[i]);
	}
}

void PID::begin(double kp[3], double ki[3], double kd[3], float ppmm[3], int min[3])
{
	outMin = -255;
	outMax = 255;
	for(byte i = 0; i < 3; i++)
	{
		Kp[i] = kp[i];
		Ki[i] = ki[i];
		Kd[i] = kd[i];
		PPMM[i] = ppmm[i];
		minPWM[i] = min[i];
	}
}

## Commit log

2025-03-13 test: uROS encoder publish topics
2025-03-13 chore: .gitignore updated
    [electronic.kicad_pcb, electronic.kicad_sch]
2025-03-13 chore: JGA MOTORS and L298N drivers added to KiCadschematic
    [electronic.kicad_sch]
2025-03-13 chore: pcd made
    [PCBZero.step, PCBZero.stl, electronic.kicad_pcb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]
2025-03-13 chore: PCB updated
    [PCBZero.step, PCBZero.stl, electronic.kicad_pcb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]
2025-03-13 chore: gerbar and images added
    [electronic materials.csv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]
2025-03-13 chore: M3 hole added to PCB
    [electronic.kicad_pcb]
2025-03-13 chore: images updated
    [electronic.kicad_pcb]
2025-03-13 chore: gerber updated
    [electronic-B_Cu.gbr, electronic-B_Mask.gbr, electronic-B_Paste.gbr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]
2025-03-13 chore: 3d files updated
    [PCBZero.step, PCBZero.stl]
2025-03-14 chore: missing 3D models added to PCB
    [ESP32-S3-DevKitC-1-N16R8V--3DModel-STEP-269445.STEP, OF-SMD5730NW--3DModel-STEP-510211.STEP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]
2025-03-14 chore: 3D model of L298N driver module added to the project
    [L298N.step, L298N.stl]
2025-03-14 chore: STL and STEP PCB files updated
    [PCBZero.step, PCBZero.stl]
2025-03-15 refactor: src dir changed
    [L298N.step, L298N.stl, PCBZero.step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]
2025-03-15 chore: PCB Lite design added to the project
    [PCBZero.step, PCBZero.stl]
2025-03-22 refactor (electronic): update PCB design
    [electronic.kicad_pcb]
2025-03-24 chore (PCB 3D.png): update img files
2025-03-24 feat(ros-ws): start urdf project, publish robot with ROS2 and gazebo
    [Link_Base.STL, Link_X.STL, Link_Y.STL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]
2025-03-25 style(model.urdf): add colors to links
    [model.urdf]
2025-03-28 chore(carobot): rename *_*.STL files to *.STL and add launcher for display the project in rviz2
    [Base.STL, X.STL, Y.STL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]
2025-03-31 fix(model.urdf): coorect position and limit of joints and links in the model
    [model.urdf]
2025-03-31 Revert "fix(model.urdf): coorect position and limit of joints and links in the model"
    This reverts commit 3ffb0695d2ab54cb5759cbb24cd0175b31b29e9f.
    [model.urdf]
2025-03-31 Reapply "fix(model.urdf): coorect position and limit of joints and links in the model"
    This reverts commit d187cfb64390a7ce33d66d2385a874b4d395dfab.
    [model.urdf]
2025-03-31 fix(model.urdf): correct position and limit of joints and links in the model
2025-03-31 fix(display.launch.py): add gui options for /opt/ros/jazzy/share/urdf_launch/launch/display.launch.py modified script
2025-04-05 feat(ros-ws/carobot): publish joint status from ROS2 (joint_state_publisher_gui) to gz by ros_gz_bridge
    [model.urdf]
2025-04-06 fix(model.urdf): correct some definitions
    [model.urdf]
2025-04-06 chore(model.urdf): test pid configurations
    [model.urdf]
2025-04-07 chore(ros-ws): edit model.urdf
    [model.urdf]
2025-04-09 refactor(ros-ws): update joint_state publisher based in data of gz sim
    [model.urdf]
2025-04-11 refactor(ros-ws): change the filename attrib in urdf to use relative directory based on the project
    [model.urdf]
2025-04-15 chore(stl): update STL files for the new design
    [X.STL, Y.STL, Z.STL]
2025-04-16 fix(model.urdf): update meshes and limits for new stl files
    [model.urdf]
2025-04-16 refactor(src): add scripts for install ROS2 and Gazebo sim
    [L298N.step, L298N.stl, PCBZero.step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]
2025-04-18 chore(electronic): update kicad files
    [electronic.kicad_pcb]
2025-04-20 fix(carobot): update model
    [model.urdf]
2025-04-29 test (yamanaka): test hardwary with arduino
2025-05-02 feat(ino/robot): add struct to control leds
2025-05-16 test (yamanaka): init PID testings
2025-05-16 test (yamanaka): config PID by mm positions
2025-05-19 fix (yamanaka): tune pulse configs
    [yamanaka.ino]
2025-05-19 feat(robot): link PID control with the GUI by ROS2
2025-05-19 refactor(robot): restructures ROS2
    [model.urdf]
2025-05-19 chore(yamanaka): replace spaces with tabs
    [yamanaka.ino]
